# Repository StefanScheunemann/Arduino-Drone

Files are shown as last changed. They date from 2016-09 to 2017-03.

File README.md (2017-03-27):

# Arduino-Drone
Eine Anleitung für den Bau eines Quadrocopters

##Inhalt  
[1. Vorwort](#Vorw)  
[2. Quellen](#Quel)  
[3. Teileliste](#Teil)  
[4. Zusammenbau](#Zusa)  
[5. Code](#Code)  
[6. PID-Kalibrierung](#PID)  
[7. Erster Start](#Erst)  
[8. Fehlercodes](#Fehler)  

###1. Vorwort
Dieser Quadrocopter ist im Rahmen eines Schulprojekts entstanden.  
Es handelt sich nicht um ein professionelles, komplett ausgereiftes Industrieprodukt und Fehler im Code sind zu erwarten. Im Umgang mit der Drohne rate ich zu großer Vorsicht. Es können durch den Quadrocopter ernsthafte Verletzungen und Schäden zugefügt werden, [hier eine realistische Einschätzung zu den Gefahren](http://www.technik-consulting.eu/Analyse/Gef%C3%A4hrdung_Drohne.html). Diese Anleitung beinhaltet Alles, was man wissen muss, um einen Quadrocopter zu bauen. Fehler oder Ungenauigkeiten können aber enthalten sein. In den Quellen können genaue Angaben gefunden werden, von welchen Stellen Code und Rahmen übernommen wurden.  

<h2>2. Quellen</h2>
<p>Der Code stammt von Herrn Brooking, eine Erklärung zu diesem und der Download können auf seiner <a href="http://www.brokking.net/ymfc-al_main.html/">Website</a> gefunden werden. Auf dieser befindet sich eine Erkärung für die Drohne.<br>
Der Code ist nicht mein Gedankengut, alle Rechte gehören Herrn Brooking. Auch die schematic für den Schaltkreis in der Drohne stammt nicht von mir und kann auf der angegebenen Webstite gefunden werden.<br>
Das verwendete 3D-Modell für den Rahmen des Quadrocopters kann auf Thingiverse <a href="http://www.thingiverse.com/thing:264955/#files">hier</a> gefunden werden, es ist für jeden frei verfügbar.<br>
Das Modell wurde nicht von mir erstellt.</p>

###3. Teileliste
In meinem Fall ist das gesamte Drohnengestell mithilfe eines 3D Druckers entstanden.  
Die dafür nötigen 3D Modelle sind repository enthalten und können frei verwendet werden. Wer keinen 3D Drucker zur Verfügung hat, kann ein fertiges Gestell kaufen, oder aus anderen Materialien selber eins bauen. Zu diesem Thema gibt es im Internet eine reichhaltige Menge an Informationen, die jederzeit abrufbar sind.  
  
Die Hardware, die benötigt wird:  
* [Arduino Uno](https://www.arduino.cc/en/Main/arduinoBoardUno)
* [Gyroscope](http://www.dx.com/p/gy-521-mpu6050-3-axis-acceleration-gyroscope-6dof-module-blue-154602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)
* [Brushless Motor + ESC combo](http://eud.dx.com/product/a2212-1000kv-brushless-motor-w-30a-brushless-esc-1045-propeller-dji-f450-550-844413446)
* [Lithium Akku](http://eud.dx.com/product/11-1v-2200mah-30c-li-polymer-battery-pack-for-450-helicopter-dji-phantom-1-450-quadcopter-844366131)
* [Akku Ladegerät](http://www.dx.com/p/b3ac-2s-3s-lipo-balance-charger-black-ac-100-240v-103589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)
* [Fernsteuerung + Empfänger](http://eud.dx.com/product/flysky-fs-t6-2-4ghz-6-ch-2-9-lcd-tx-transmitter-rx-receiver-radio-control-system-black-8-x-aa-844178448)
* Widerstände: [330](https://www.conrad.de/de/metallschicht-widerstand-330-axial-bedrahtet-0207-06-w-yageo-mf0207fte52-330r-1-st-1417595.html), [1k](https://www.conrad.de/de/metallschicht-widerstand-1-k-axial-bedrahtet-0207-06-w-yageo-mf0207fte52-1k-1-st-1417606.html), [1,5k](https://www.conrad.de/de/metallschicht-widerstand-15-k-axial-bedrahtet-0207-06-w-1-st-423386.html)
* [Schrumpfschlauch](https://www.amazon.de/ChiliTec-12000058-Chilitec-Schrumpfschlauch-Sortiment-100-teilig/dp/B003H9CJ1Y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) (nicht zwingend nötig, hilft aber beim Isolieren)

###4. Zusammenbau<a name="Zusa"><a/>
Zuerst wird der Rahmen des Quadrocopters zusammengebaut.  
Jeder Rahmen ist unterschiedlich aufgebaut. Im Fall des beigelegten Rahmens ist der Aufbau leicht verständlich. Es ist sinnvoll, die untere Platte vorerst nicht zu befestigen, da es dann einfacher ist, die Elektronik einzubauen.  
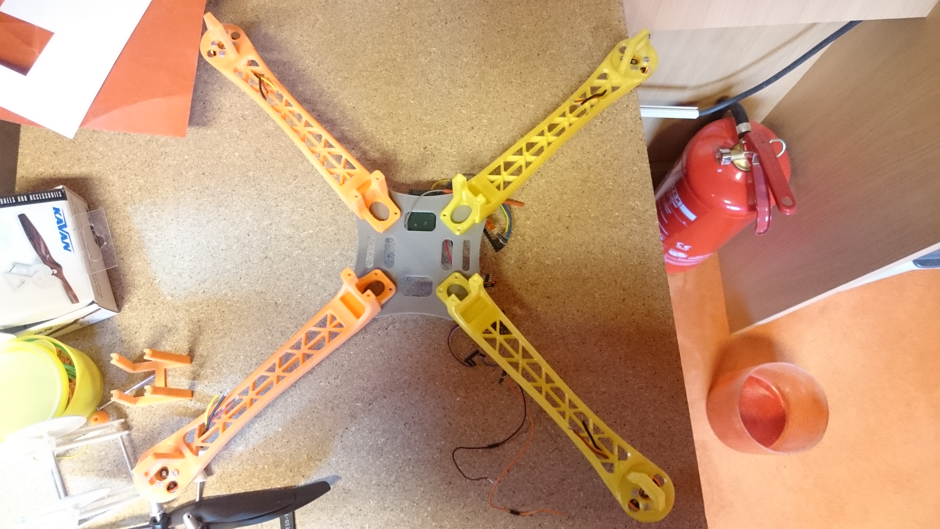
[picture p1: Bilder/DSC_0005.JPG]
  
Sobald der Rahmen zusammengesetzt ist, kann die Hardware verbaut werden.
Der Quadrocopter kann mit den Teilen aus der [Teileliste](#Teil) gebaut werden, aber auch äquivalente Bauteile sollten funktionieren.  
Bei der Verkabelung ist darauf zu achten, dass die schematics beachtet werden, da es sonst später zu Fehlfunktionen kommen kann.  
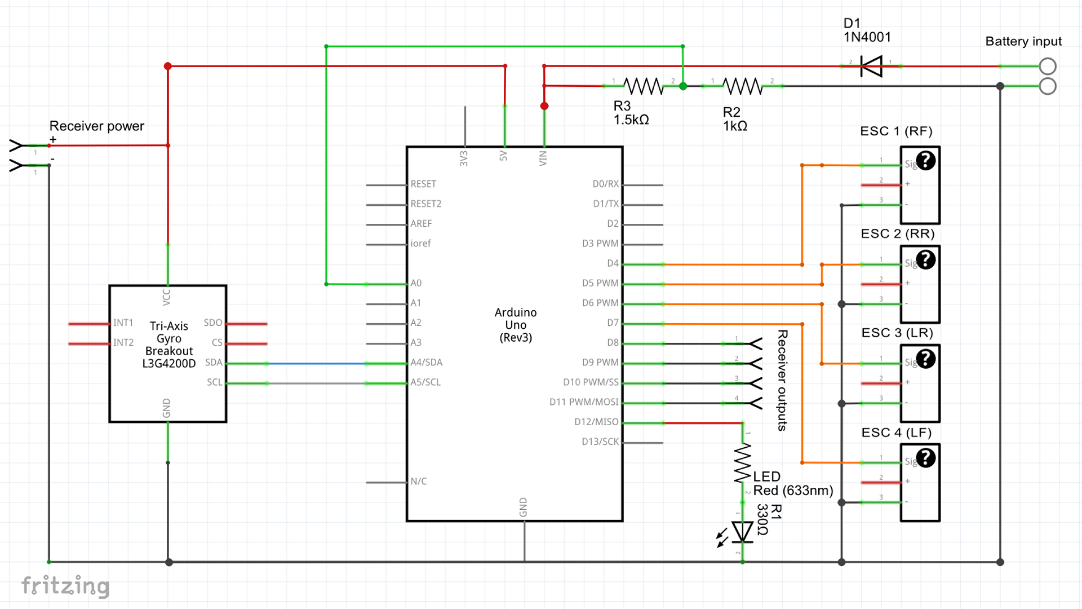
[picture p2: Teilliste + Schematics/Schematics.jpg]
  
Es ist am einfachsten, mit den ESCs zu beginnen.
Diese sollten möglichst weit vom Zentrum entfernt sein, da sie sonst später das Gyroskop stören könnten.
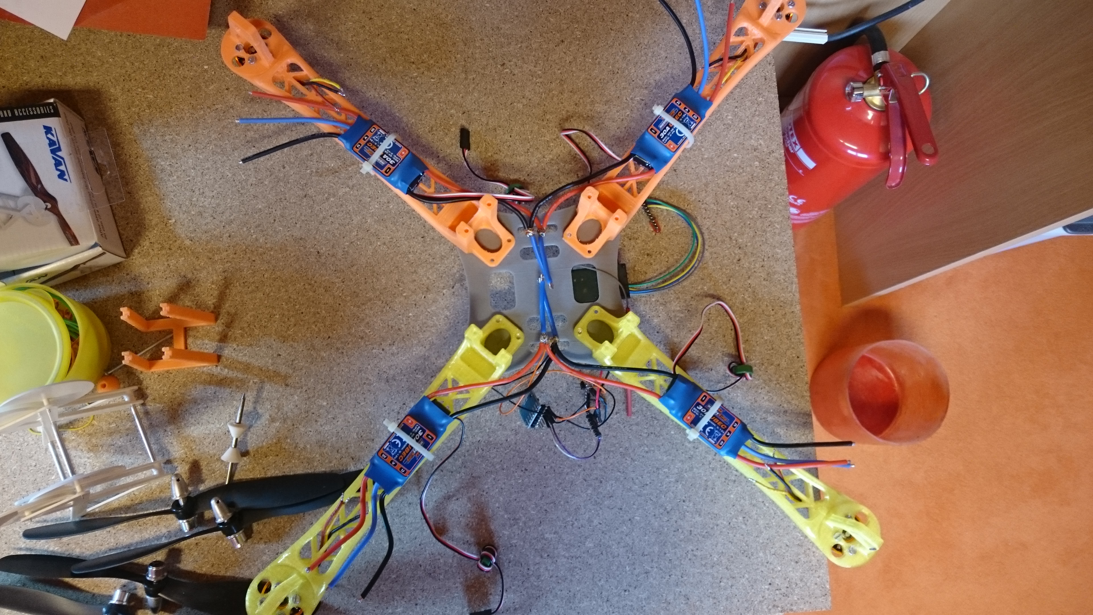
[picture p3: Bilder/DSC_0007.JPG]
  
Sobald die ESCs befestigt sind, dreht man den Rahmen um und befestigt nur das Gyroskop und den Empfänger. Doppelseitiges Klebeband ist für diesen Zweck geeignet. Die Kabel an diesen Teilen sollten schon vor dem Befestigen am Rahmen festgelötet werden, da dies anderenfalls schwierig werden könnte.  
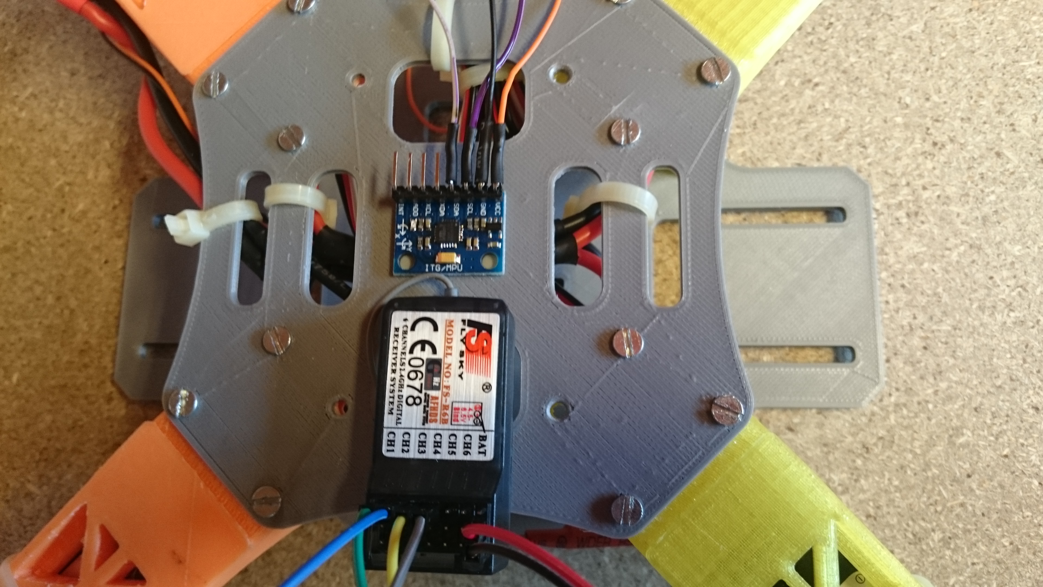
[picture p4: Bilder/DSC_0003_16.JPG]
  
Im nächsten Schritt wird das Arduino befestigt. Wie genau das Arduino am Rahmen befestigt werden kann, muss jeder an seinem eigenen Rahmen überprüfen. Wenn der Rahmen aus den 3D Modellen verwendet wird, ist eine spezielle Platte für diesen Zweck enthalten.  
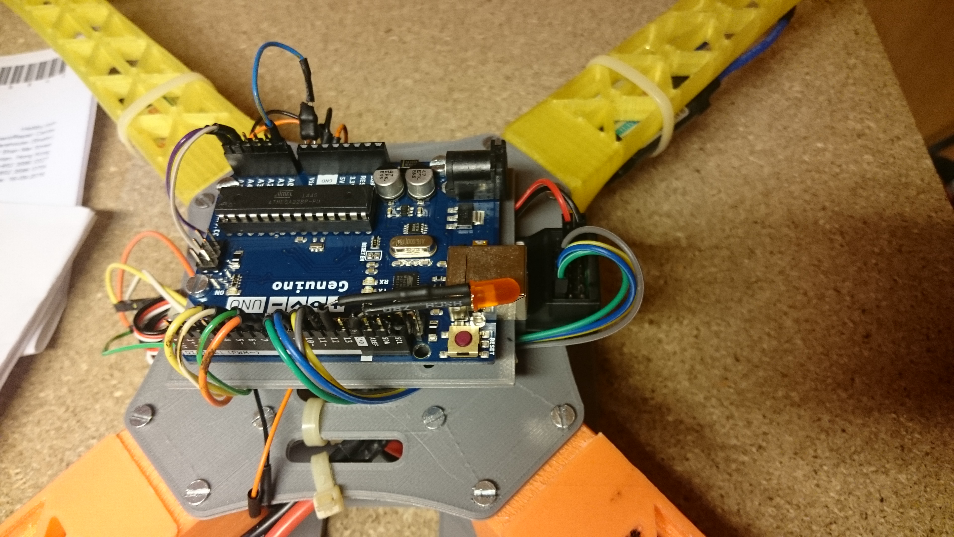
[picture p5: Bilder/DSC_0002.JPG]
  
Als Letztes werden die Motoren befestigt. Dabei muss auf die Rotationsrichtung geachtet werden. Brushless Motoren besitzen drei Ausgänge, ein rotes Kabel, welches den Pluspol darstellt, ein schwarzes Kabel, welches den Minuspol darstellt und ein drittes Kabel als Erdung, häufig gelb. Uns interessieren das Plus- und das Minuskabel. Wenn man Positiv mit Positiv am ESC verbindet und Negativ mit Negativ, dreht sich der Motor im Uhrzeigersinn. Wenn Positiv mit Negativ und Negativ mit Positiv verbunden wird, dreht sich der Motor  gegen den Uhrzeigersinn. In allen Fällen muss auch das dritte Kabel angeschlossen werden. Dies sollte immer an sein Äquivalent des ESCs angeschlossen werden.  
Es muss darauf geachtet werden, dass die Richtungen der Motoren stimmen, da der Quadrocopter später sonst nicht fliegen kann. 
  
| Motor | Bezeichnung | Richtung |
|---|:---:|:---:|
| vorne rechts  | Motor 1 | Uhrzeigersinn |
| hinten rechts | Motor 2 | gegen Uhrzeigersinn |
| hinten links  | Motor 3 | Uhrzeigersinn |
| vorne links | Motor 4 | gegen Uhrzeigersinn |  
  
In der Praxis sieht es wie auf den folgenden Bildern aus.  
Uhrzeigersinn  
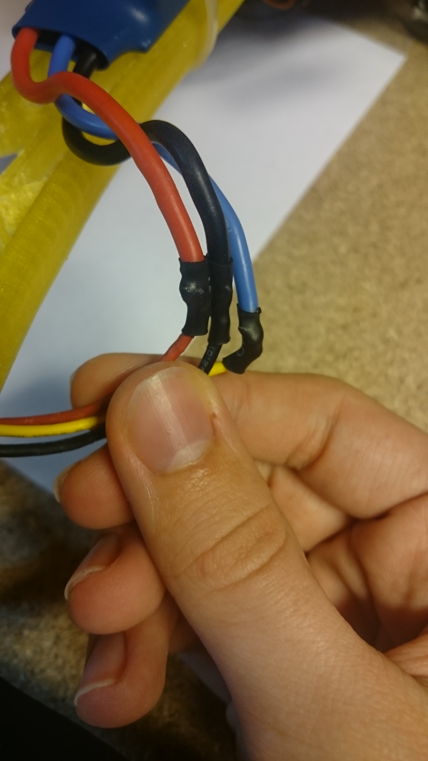
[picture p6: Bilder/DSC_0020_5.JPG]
  
Gegen Uhrzeigersinn  
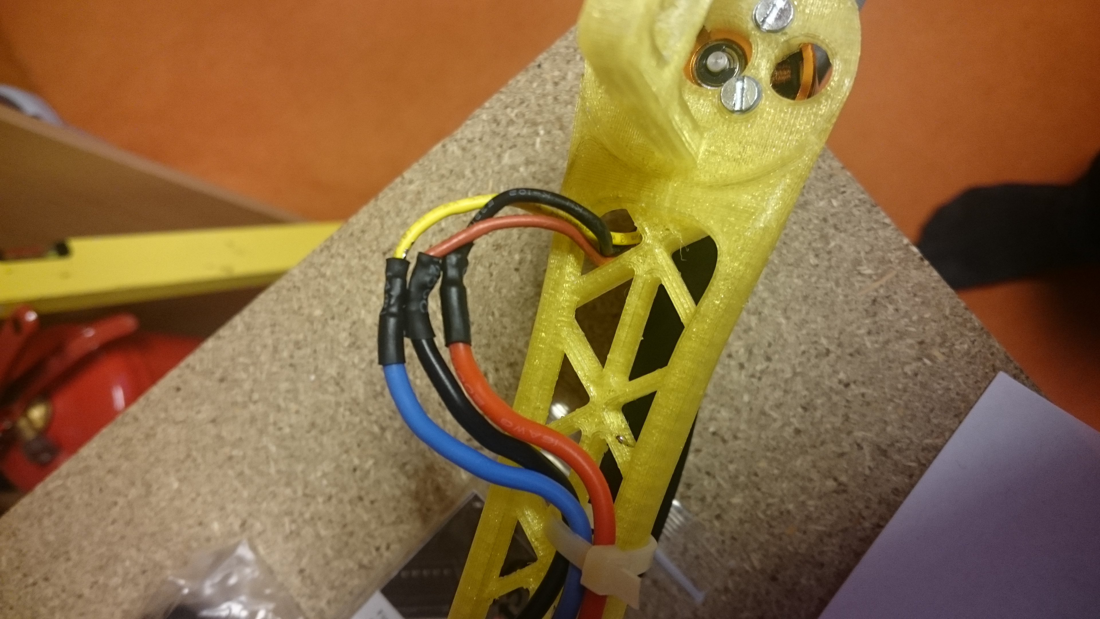
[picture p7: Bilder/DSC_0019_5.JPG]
  
  
Jetzt ist die gesamte Hardware verbaut. Im nächsten Schritt wird diese verkabelt.  
Ich empfehle, alle Verbindungen zu löten, da so eine feste Verbindung entsteht. Aber auch z.B. Kabelhülsen funktionieren. In jedem Fall muss sich streng an die schematics gehalten werden!  
Zum besseren Verständis der Verbindungen  
Verbindung der ESCs, falls der Rahmen kein PDB (power distribuition board) enthält  
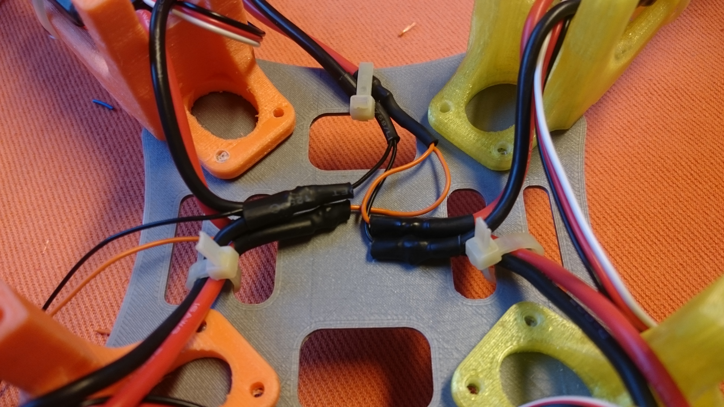
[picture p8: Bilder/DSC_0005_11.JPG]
  
Kabel am Arduino  
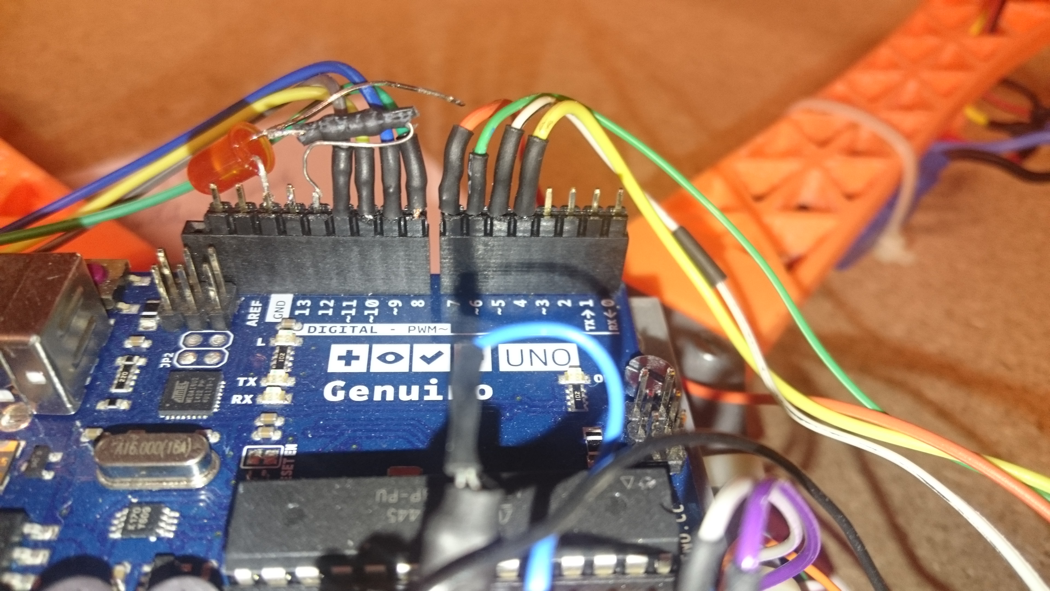
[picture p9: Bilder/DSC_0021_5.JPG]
  
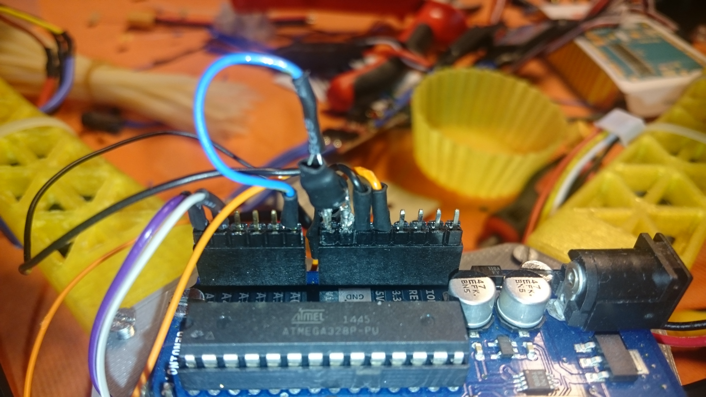
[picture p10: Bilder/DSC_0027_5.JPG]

  
Abschließend ist es von Vorteil, über das Arduino einen Schutz anzubringen, damit es nicht ungeschützt beim Transport bzw. Flug ist. Bei den 3D Modellen liegt ein derartiger Schutz bei, ob man diesen verwendet oder selber etwas anderes baut, spielt keine große Rolle, solange es gegen Einwirkungen von außen schützt.  
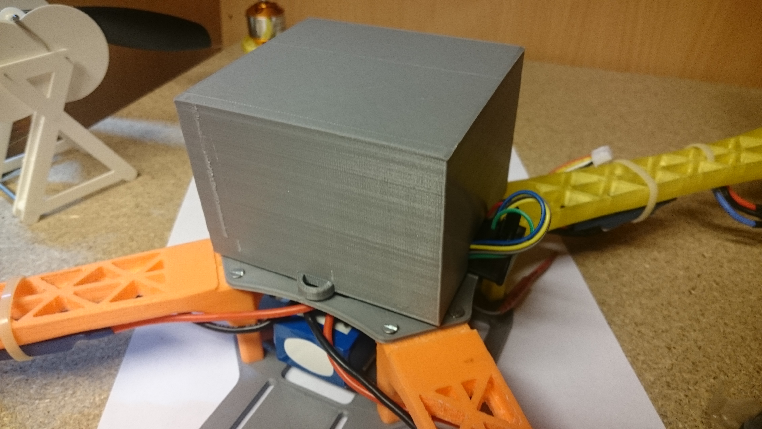
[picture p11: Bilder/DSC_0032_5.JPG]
  

###5. Code<a name="Code"><a/>
Um die Drohne verwenden zu können, werden drei Arduino Sketches benötigt.  
[1. Setup](#Setup)  
[2. Calibration](#Calib)  
[3. Flight Controller](#Flight)  
  
Der erste Sketch ist ein Setup, in dem alle Bauteile der Drohne überprüft werden und sowohl die Fernbedienung, als auch das Gyroskop für das Arduino kalibiriert werden. Die Ergebnisse der Kalibrierungen werden im EEPROM, dem Speicher des Arduinos, gespeichert. Das Programm läuft über den seriellen Monitor des Arduinos.    
Der zweite Sketch wird verwendet, um die Ergebnisse der Kalibrierung zu testen. Im seriellen Monitor können durch bestimmte Befehle unterschiedliche Daten aufgerufen werden. Darauf gehe ich aber erst im letzten Teil dieser Anleitung ein, da dies sonst zu umfangreich wird: [Der erste Start](#Erst).  
Der dritte Sketch ist der flight controller. Mit diesem wird die Drohne letztlich gesteuert. Es ist eine Sicherungsfunktion enthalten. Aber trotzdem sollte beim Start immer ein Sicherheitsabstand eingehalten werden.  
Alle diese drei Sketches müssen vom Ersten bis zum Dritten auf den Arduino geladen werden, ausgeführt werden und nur wenn keine Fehler während der Prgrammabläufe auftauchen, darf das Nächste installiert werden. Bei Nichtbeachtung der Reihenfolge kann es zu schweren Fehlern kommen.  
  
Zum Grundverständnis erkläre ich an dieser Stelle erstmal, wie der Quadrocopter seine Position und die Befehle der Fernbedienung "versteht". Im folgenden Text wird häufig von einem Puls zwischen 1000 und 2000 gesprochen. Dieser Puls bedeutet eigentlich nur, dass die Fernbedienung die Befehle mit einer Frequenz von 1000 bis 2000 Hertz an den Empfänger sendet. Das Arduino rechnet auch mit dieser Frequenz. Es wäre auch möglich, dies in ein kleineres Format im Arduino für die Rechnungen umzuwandeln. Das Ergebnis wäre aber dasselbe und würde innerhalb des Codes zu Verwirrung führen. Während des Setups wird auch an die ESCs diese Frequenzreichweite übertragen, da diese auch mit Pulsen arbeiten. Wenn eine Reichweite von 1000 mögliche Pulsen existiert, ist auch eine sehr genaue Bestimmung der Werte möglich und sehr genaue Ergebnisse können innerhalb des Codes produziert werden.  
Die Werte 1000 bis 2000 sind also nicht frei erfunden und nur als Variablen festgelegt, sondern durch die Fernbedienung definiert und müssen so verwendet werden.  
  
Der gesamte Code kann eingesehen und modifiziert werden. Der Code ist durch viele Kommentare verständlich gemacht. Inwiefern Modifikationen sinnvoll sind und wo diese vorgenommen werden sollten, wird im späteren Verlauf dieser Dokumentation aufgegriffen.  
Direkte Weiterleitungen zum Code:  
  
[Setup](https://github.com/StefanScheunemann/Arduino-Drone/tree/master/Code/Setup)  
[Calibration](https://github.com/StefanScheunemann/Arduino-Drone/tree/master/Code/Calibrate)  
[Flight controller](https://github.com/StefanScheunemann/Arduino-Drone/tree/master/Code/Flight_controller)  
  
####Setup<a name="Setup"><a/>
Im Setup wird die gesamte Hardware für das Arduino kalibriert. Um dies zu tun, muss der Setup-Sketch auf den Arduino geladen werden und am PC im Arduino-Programm der serielle Monitor geöffnet werden. Im seriellen Monitor muss die Baudrate auf 57600 eingestellt werden für diesen Vorgang.  
Falls während des Setups Fehler auftreten, wird ein Fehlercode angezeigt. Jeder Fehler ist dokumentiert und mit Lösungen versehen. Diese Lösungen werden im späteren Verlauf dieser Anleitung dokumentiert. [Abkürzung zu Fehlercodes](#Fehler)  
Nun wird ein Programm Ablauf gezeigt, dem man als Nutzer nur folgen und die Befehle befolgen muss.  
Zuerst werden die Endposition der Fernbedienung kalibriert. Dabei ist zu beachten, dass "nose down" auf dem rechten Steuerknüppel "nach unten" bedeutet. Wenn der Quadrocopter seine Nase hoch zieht, bewegt der Quadrocopter sich nach hinten.  
Sobald die Kalibrierung der Fernbedienung abgeschlossen ist, beginnt die Kalibrierung des Gyroskops. Zu diesem Zweck wird das Programm den Nutzer dazu auffordern, den Quadrocopter in bestimmte Positionen zu bewegen. Dabei muss darauf geachtet werden, dass die richtigen Seiten bewegt werden, da es sonst später zu Fehlern kommen kann.  
Der letzte Schritt ist die Kontrolle der Status-LED. Diese sollte aufleuchten, wenn der Befehl dazu im seriellen Monitor angezeigt wird. Prinzipiell ist die LED nicht nötig. Falls aber später Probleme auftreten, kann an der Blinkfrequenz erkannt werden, um welchen Fehler es sich handelt. Die LED erfüllt somit eine wichtige Rolle.  
  
Nun sollte das Programm anzeigen, dass der Vorgang beendet ist und der serielle Monitor kann geschlossen werden.  
An dieser Stelle ist das Setup abgeschlossen. Es kann zum nächsten Schritt übergegangen werden.  
Wer aber noch daran interessiert ist, wie der Code aufgebaut ist und wie die Informationen im EEPROM gespeichert werden, kann den Code frei verwenden und modifizieren, alle Informationen sind Open Source und es darf daran alles verändert werden. Doch macht es in diesem Sketch wenig Sinn, etwas zu modifizieren.  
Im späteren Verlauf wird das Modifizieren noch wichtiger.  
Der Code ist zum besseren Verständis mit Kommentaren versehen. Es sollte nicht nötig sein, sich aufwändig einlesen zu müssen, um den Inhalt zu verstehen.  
  
#####Calibration<a name="Calib"><a/>
Das zweite Programm, welches installiert werden muss, ist die Kablibrierung.  
Dieser Sketch unterscheidet sich stark vom Setup. Es wird nichts auf dem EEPROM verändert.  
Sobald der Sketch auf den Arduino geladen ist, muss wieder der serielle Monitor geöffnet werden. Es wird weiterhin die Baudrate 57600 verwendet.  
Nun gibt es mehrere Befehle, die ausgeführt werden können, zum Überprüfen der Funktionen des Gyroskops, der Fernbedienung und der Schwingungen der Motoren.  
Wenn in den seriellen Monitor **a** eingegeben wird, zeigt der serielle Monitor die Position des Gyroskops. Zu beachten ist, dass Yaw bedeutet, inwieweit der Quadrocopter auf dem Boden gedreht wurde. Sobald die Drehung beendet ist, setzt der Wert für Yaw sich selbstständig auf 0 zurück. Es sollte eine perfekte Nullstellung erreicht werden, da der Quadrocopter sonst nie ruhig in der Luft stehen kann.  
  
Als nächstes wird in den seriellen Monitor **r** eingegeben. Mit diesem Befehl werden die Daten der Fernbedienung aufgerufen. Im seriellen Monitor werden nun vier unterschiedliche Daten angezeigt.  
  
Die Werte sollten sich zwischen 1000 und 2000 befinden, der Anstieg/Abfall der Werte sollte gleichmäßig sein und nicht springen, da es sonst später zu Problemen kommen kann. Minimale Abweichungen sind unproblematisch. Es sollten nur keine großen Abweichungen sein.  
  
Mit den Befehlen **1-5** kann entwededer von jedem Motor einzeln die verursachte Vibration überprüft werden. Zu diesem Zweck sollte auf den Motoren ein Propeller befestigt werden. Im Idealfall liegt die Vibration unter 50. Dies ist kein Referenzwert, der mit anderen Werten verglichen werden kann. Der Test sollte bei 50 % Beschleunigung ablaufen. In dieser Position sollte der Quadrocopter knapp nicht abheben und es werden gute Ergebnisse erzeugt. Bei diesem Test ist größte Vorsicht geboten, der Quadrocopter kann schwere Verletzungen zufügen und es sollten mindestens **fünf Meter** Sicherheitsabstand eingehalten werden; ideal sind **zehn Meter**.
  
| Motor	 | Command |
|---|:---:|
| Motor 1	  | 1 |
| Motor 2 | 2 |
| Motor 3	  | 3 |
| Motor 4	  | 4 |
| Motor 1-4 | 5 |
  
####Flight Controller<a name="Flight"><a/>
Das dritte Programm ist das, dass letztendlich für das Fliegen verwendet wird. Dieser Sketch greift auf die Daten, die im EEPROM abgelegt wurden, zurück und verwendet sie als Grundlage der Berechnungen für die Stabilität. Die vorherigen Schritte müssen genau befolgt werden, da sonst Fehler beim Flug entstehen können.  
  
Das Gyroskop gleicht beim Flug permanent den Quadrocopter aus, sodass zu keinem Zeitpunkt, wenn kein Befehl, abgesehen von der senkrechten Beschleunigung, übertragen wird, der Quadrocopter in eine nicht horizontale Position gerät.  
Der Ablauf im Sketch hinter dieser Mechanik ist, dass das Gyroskop permanent die Position des Quadrocopters überprüft. Im Sketch ist festgelegt, dass in der Nullstellung des Gyroskops und der Fernbedienung ein Puls von 1500 an die ESCs gesendet wird. Nullstellung bedeutet, dass der Quadrocopter senkrecht zum Boden ausgerichtet ist. Die ESCs sind auf die Frequenz von 1000 bis 2000 kalibiriert.  
Wenn nun der Winkel, in dem sich der Quadrocopter relativ zum Boden befindet, verändert wird, rechnet das Arduino eine definierte Antisteigung aus; also die aktuelle Position abgezogen von der Standardposition und ermittelt einen Gegenimpuls, der an die ESCs geschickt wird.   
Im Sketch ist festgelegt, dass wenn die senkrechte Beschleunigung, also der linke Steuerknüppel, in der untersten Position ist, der Quadrocopter 0 % Motor-Output aufbringt. Der Output steigt linear bis auf 100 % in Maximal-Stellung an. Wichtig ist dabei zu wissen, dass bei 50 % der Quadrocopter stabil in der Luft steht und weder steigt noch sinkt. Bei unter 50 % wird ein Absinken und bei über 50 % ein Ansteigen zu beobachten sein. Falls dies nicht richtig funktioniert, müssen die Fernbedienung und der Quadrocopter neu kalibriert werden. Das Kalibrieren des Quadrocopters muss erneut über das Setup durchgeführt werden und sollte nicht übersprungen werden.   
  
Wenn der Quadrocopter sich also in der Ausgangslage befindet, wird ein Puls von 1500 an den PID-controller gesendet (dieser wird im [nächten Teil](#PID) genauer erklärt) und es wird keine Veränderung vorgenommen. Wenn nun aber auf der Fernbedienung der Befehl Roll gegeben wird mit halber Beschleunigung, also der rechte Steuerknüppel 50 % nach rechts gedrückt wird, so wird der Wert auf 1750 erhöht. Nun kippt der Quadrocopter kontinuierlich nach rechts. Das Gyroskop nimmt diese Veränderung der Lage wahr und rechnet seine eigene Rechnung dagegen. Im Code ist festgelegt, das für jeden 1°, den der Quadrocopter gekippt ist, ein Puls von 15 gegengerechnet wird. Wenn beim Rollen nun also 5° erreicht sind, wird gegen die 1750, die von der Fernbedienung ausgegeben werden und vom Arduino verwendet werden, ein Wert von 75 gegengerechnet. Der interne Wert für die Position ist nun also 1675. Das Rollen wird soweit weitergeführt, bis der Wert von 1500 erreicht und und der Quadrocopter damit seine Zielposition, die er immer erreichen möchte, erreicht hat. Dieser Fall tritt in diesem Fall bei 16,7° ein. Wenn man also den Befehl fürs Rollen mit 50 % Leistung gibt, wird der Quadrocopter bis auf 16,7° kippen und in dieser Position bleiben, bis ein neuer Befehl von der Fernbedienung gegeben wird. Maximal möglich sind 33,3°. Dieser Wert wird als allgemein sicher anerkannt und führt zu guter Beschleunigung und gut kontrollierbarem Flugverhalten. Weiteres Rollen würde zu höherer Beschleunigung führen, aber auch die Gefahr eines Überschlags erhöht sich. Diese Werte gelten genauso für Pitch und Yaw, nur die senkrechte Beschleunigung ist nicht von dieser Berechnung betroffen.  
  
Wenn der Maximalwinkel größer/kleiner sein soll, muss am Code eine Veränderung vorgenommen werden. Dies ist in Zeile 14 und 22 des flight controllers möglich. Wenn der Wert erhöht wird, steigt der maximale Winkel. Wenn der Wert verkleinert wird, sinkt der maximale Winkel. Es kann sinnvoll sein, den Winkel zu verkleinern, wenn die Drohne dem Nutzer zu aggressiv reagiert.  
Auch der Standardwert von α=1°=15 kann verändert werden. An diesem Wert zu modifizieren ist eher nicht empfehlenswert, da der Quadrocopter selbst bei kleinen Veränderungen sehr aggressiv reagieren kann. Wenn der Maximalwinkel verändert werden soll, ist es sinnvoller, die vorherige Methode zu verwenden.  
  
Falls der Quadrocopter anders reagiert, als man es erwarten würde und das Problem mit dem Gyroskop in Verbindung stehen könnte, kann die gesamte auto level Funktion deaktiviert werden. Dies ist in Zeile 24 möglich. Es ist wichtig zu bedenken, dass mit dieser Einstellung auf false keine Flugunterstützung mehr existiert. Es muss manuell gegengelenkt werden. Im Allgemeinen rate ich von einem Flug ohne auto level-Funktion ab.  
  
Im flight controller ist noch eine weitere Funktion eingebaut, die die LED verwendet.  
Die LED zeigt einen niedrigen Akkustand an, indem sie beginnt, durchgehend zu leuchten. Die Funtion dafür befindet sich in Zeile 250.   Wenn die output-Spannung des Akkus zu niedrig wird, um die Motoren mit ausreichend Energie versorgen zu können, beginnt die LED permanent zu leuchten. Diese Warnung bedeutet nicht, dass der Quadrocopter nicht mehr fliegen kann. Er sollte aber in absehbarer Zeit gelandet werden.  

Darüber befindet sich eine Funktion, die es für den Arduino einfacher macht, durch einen komplementären noise filter den Akkustand zu errechnen. Mit diesem treten weniger Ungenauigkeiten beim Errechnen der Spannung des Akkus auf und die LED zeigt nicht schon zu früh einen niedrigen Akkustand an.  
  
Falls noch weitere Unklarheiten bezüglich des flight controllers existieren kann jede Einzelheit [hier](https://github.com/StefanScheunemann/Arduino-Drone/tree/master/Code/Flight_controller) im Code nachgelesen werden. Der gesamte Code ist mit Kommentaren zum besseren Veständnis gefüllt.  

##6. PID Kalibrierung<a name="PID"><a/>
Die PID Werte sind das Erste, was man sehen wird, sollte man den Code des flight controllers öffnen.  
Diese PID Werte sind essentiell für die auto level-Funktion des Quadrocpters, die das Besondere an diesem gesamten Projekt ist. Zum Verständis ist es als erstes sinnvoll zu verstehen, wofür PID steht. Wer schnell zu dem Teil springen möchte, in dem erklärt wird, wo und wie man diese Werte anpassen sollte, wird [hier](#PIDmod) weitergeleitet.  
  
####Theoretische Erklärung der PID-Werte  
  
**P** steht für proportinal, an dieser Stelle wird **Output des Gyroskops - Output des receivers * P(gain)** gerechnet, oder auch  
(gyro - receiver) * P (gain). Wenn sich nun der Quadrocopter in einer 10°-Lage gekippt zum Boden befindet und 1°=15 => 10*15=150. Nehmen wir nun an, von der Fernbedienung wird kein Befehl gesendet, der eine solche Veränderung der Lage herbeiführt, so wird der Quadrocopter nun versuchen, in die Standardposition von 1500 zurück zu kehren. Aus der Rechnung ergibt sich also, dass der aktuelle Wert 1650 entspricht, aber 1500 angepeilt werden. Theoretisch sollte diese Funktion ausreichen, um den Quadrocopter in eine stabile Position zu bringen. Wenn man aber nur diese Funktion verwendet, so wird man feststellen, dass der Quadrocopter anfängt, gleichmäßig zu schwingen. Bei jeder Korrektur wird der Quadrocopter von selbst übersteuern und nie in eine ruhige Position kommen. Um dieses Problem zu lösen werden weitere Funktionen eingebracht, die auf einer anderen Basis den Quadrocopter stabilisieren.  
  
**I** steht für Intergral, in dieser Funktion wird  
I(output) + ((gyro - receiver) * I(gain). Wenn man nun also wieder von 10° relativer Steigung Nullpunkt ausgeht, dann wird bei einem Wert von I = 1 die Rechnung I(output), jetzt noch 0 + ((150 - 0), da von der Fernbedienung kein Befehl gesendet wird, * I(gain), was als 1 definiert wurde, gerechnet und es kommt ein Ergebnis von 150 raus, was der Korrketur entspricht, die ausgeführt werden muss.  
In der nächsten Rechnung wird 150(der output der letzten Rechnung) + ((150 - 0) * I(gain, was als 1 definiert bleibt), gerechnet.  
Im Ergebnis bedeutet dies, dass selbst wenn die Steigung konstant ist und der Winkel nicht verändert wird, die Korrektur immer stärker wird, bis wieder der Nullpunkt erreicht ist, an der der errechnete Wert wieder auf 0 zurücksetzt wird, da sobald der Winkel = 0° ist und von der Fernbedienung kein Befehl gesendet wird, das Ergebnis der Rechnung gleich 0 ist.  
Wenn nur diese Rechnung verwendet wird, kann wieder festgestellt werden, dass der Quadrocopter überkompensiert und somit immer noch keine stabile Haltung in der Luft erreicht werden kann. Der Quadrocopter wird mit nur dieser Funktion, ähnlich wie bei der ersten von einer Seite zur anderen schwingen. Doch dies passiert deutlich langsamer. Um nun eine stabile Position zu erreichen, ist eine weitere Funktion nötig, die das Überkompensieren verhindert.  
  
**D** steht für Derivative, diese Funktion unterscheidet sich von den vorherigen, als dass sie nur auf eine Veränderung eine einmalige Korrektur ausgibt und nicht, wie die anderen Funktionen, konstant gegen die Steigung gegenarbeitet.  
(gyro - receiver - gyro(prev) - receiver(prev)) * D(gain). Wenn man nun wieder davon ausgeht, dass D = 1 definiert ist, dann ergibt sich bei einer Steigung von 10° im Intervall davor eine Steigung von 0°
(150 - 0 - 0 - 0) * 1, das Ergebnis wäre eine Korrektur von 150. Wenn man nun aber im nächsten Messintervall weiterhin die Position von 10° verwendet, dann ergibt sich  
(150 - 0 - 150 - 0) * 1, das Ergebnis dieser Rechnung wäre 0. Diese Funktion verursacht also nur eine Korrektur, wenn die Position zwischen zwei Intervallen sich verändert, ansonsten ist das Ergebnis immer 0.  
Wenn nun durch die anderen beiden Funktionen eine Überkompensation stattfindet, dann sendet diese Funktion eine einzelne Korrektur, die den Quadrocopter wieder ausgleicht und in die waagerechte Position regelt.  
  
Um es anschaulicher zu machen habe ich eine Google-Tabelle mit den Rechnungen erstellt. Die Diagramme zeigen die Korrekturbefehle, die von den Funktionen gesendet werden. Auch kann das Dokument heruntergeladen werden und mit den PID-Werten experimentiert werden, wie diese sich verändern, wenn die gain-Werte verändert werden. In dem Dokument liegen zwischen jedem Messungsinvtervall 4 Millisekunden. Mit diesem Wert arbeitet auch das Arduino im flight controller. Die Rechnungen des PID controllers finden im flight controller in Zeile 424 statt, das Verändern der PID-Werte wird aber in Zeile 9 - 11 durchgeführt.  
  
**[Link zur Tabelle](https://docs.google.com/spreadsheets/d/1bJNEvERLeVwe6B2JFlEnVjHe6nW1A6QOTmVpb9kBsjY/edit?usp=sharing)**  
  
Praktische Anwendung der PID Werte<a name="PIDmod"><a/a>  
  
Wenn man nun weiss, wie der PID controller funktioniert, kann man beginnen, die gain-Werte zu modifizieren.  
Jeder Quadrocopter hat eine andere Struktur und reagiert anders auf die Korrekturen. 
Deswegen **müssen** die PID-Werte manuell angepasst werden und nach jedem Umbau oder größerer Reperatur muss die Kalibrierung neu erfolgen.  
Die im Programm angegebenen PID-Werte sind nicht allgemein gültig. Mein Quadrocopter funktioniert mit diesen aber am besten.  
  
Für die folgende Prozedur empfehle ich, im ersten Teilschritt bei der Kalibrierung des D-Wertes Sicherheitshandschuhe anzuziehen, um Verletzungen zu vermeiden.  
  
Um die Kalibrierung zu beginnen, müssen im flight controller die PID-Werte für roll, Zeile 9 bis 11) auf 0 gesetzt werden. Die Kalibrierung verläuft am besten, wenn man mit dem D-Wert beginnt. Dies tut man, indem in Zeile 11 der Wert für D nun von 0 auf 3 erhöht wird. Mit dieser Veränderung wird der Sketch auf den Quadrocopter übetragen. Nun greift man den Quadrocopter fest in der Mitte und beginnt den Schub zu erhöhen. Der Schub wird solange erhöht, bis der Punkt erreicht ist, an dem der Quadrocopter **fast** vom Boden abhebt. Jetzt muss der Quadrocopter in alle Richtungen geneigt werden, der Quadrocopter sollte sich stabil anfühlen und nicht ruhelos. Nun erhöht man den D-Wert immer weiter in Schritten von 1 und testet jedes Mal, bis der Quadrocopter sich unruhig anfühlt und beginnt, sich ungleichmäßig zu verhalten. Die Unruhe sollte bei +-20 einsetzen. Wenn dieser Punkt erreicht ist, zieht man vom D-Wert 25 % wieder ab und erhält einen Wert, bei dem der Quadrocopter sich ruhig verhält.  
  
Als nächstes wird dieser Vorgang für den P-Wert wiederholt. Statt einer Erhöhung von 1 pro Versuch, sollte diesmal eine Steigerung von 0.2 verwendet werden. An diesem Punkt muss der Quadrocopter auch nicht mehr in der Hand gehalten werden. Auf einer Grasfläche kann vorsichtig geflogen werden. Wenn wieder der Punkt erreicht ist, an dem der Quadrocopter sich unruhig verhält, wird der Wert um 50 % reduziert und erhält somit einen stabilen P-Wert.  
  
Im letzten Schritt wird der I-Wert erhöht. Dies findet in Schritten von 0.01 statt. Man wird feststellen, dass der Quadrocopter immer stabiler fliegt. Wieder wird der Quadrocopter ab einem bestimmten Wert sich unruhig verhalten. An diesem Punkt wird der I-Wert wieder um 50 % reduziert.  
  
Wenn diese Kalibrierung abgeschlossen ist, erhält man einen stabil fliegenden Quadrocopter. Es darf aber nicht vergessen werden, dass nach jedem Umbau und jeder Reparatur diese Prozedur wiederholt werden sollte.  

##7. Erster Start<a name="Erst"><a/>
Sobald der Sketch auf dem Arduino gespeichert ist, ist die Drohne flugbereit. Beim Start gilt es bestimmte Dinge zu beachten:  
1. Um den Quadrocopter zu starten, muss an der Fernbedienung der throttle stick in die untere, linke Ecke bewegt werden. Erst ab diesem Moment ist Sicherung deaktiviert.  
2. Um den Quadrocopter auszuschalten, muss der throttle stick in die untere, rechte Ecke bewegt werden. Dies löst die Sicherung aus und keine weiteren Befehle werden umgesetzt.  
3. Sobald die Sicherung deaktiviert ist, muss der Quadrocopter gestartet werden. Die ersten Sekunden ist der Ausgleich durch das Gyroskop deaktiviert, sodass die Drohne senkrecht starten kann. Sie gleicht sich erst in der Luft aus. Auch sollte insofern zügig gestartet werden, damit ein schnelles Abheben auf mindestens 20 Centimeter gewährleistet ist und die Drohne sich nicht am Boden verfangen kann.
4. Vor und während des Fluges ist ein Sicherheitsabstand einzuhalten. Ein Start aus der Hand ist zwingend zu vermeiden, da durch Windstöße oder Fehler des Programms die Drohne aggressiv reagieren kann und somit den Nutzer schwer verletzen kann.  
5. Es ist durchaus damit zu rechnen, dass erste Flugversuche fehlschlagen. Es sollte von Beginn an eingeplant werden, dass einige Propeller kaputt gehen. Die gegebenen PID-Werte sollten einen stabilen Flug gewährleisten, es können aber dennoch Probleme auftreten. Um diese Probleme zu beheben, müssen die PID-Werte angepasst werden. Wie dies möglich ist, wurde im [vorherigen Teil](#) erklärt.  
6. Die eingebaute LED hat zwei Funktionen. Wenn die LED permanent leuchtet, bedeutet dies, dass der Akku unter 25 % Leistung gefallen ist. Wenn die LED schnell blinkt, konnte keine Verbindung hergestellt werden. In diesem Fall sollte einige Sekunden gewartet werden.  
  
Wenn der erste Flug erfolgreich verlaufen ist, sollten alle Teile des Quadrocopter überprüft werden. Selbst bei einem erfolgreichen Flug können Schäden entstehen. Der Rahmen sollte besonders genau betrachtet werden, da durch die Motoren starke Kräfte auf diesen ausgeübt werden. Falls Risse oder ähnliche Schäden auftreten, müssen diese behoben werden. Es darf nicht mit defekten Teilen geflogen werden.  
  
Ein derartiger Riss kann zum Beispiel so aussehen  
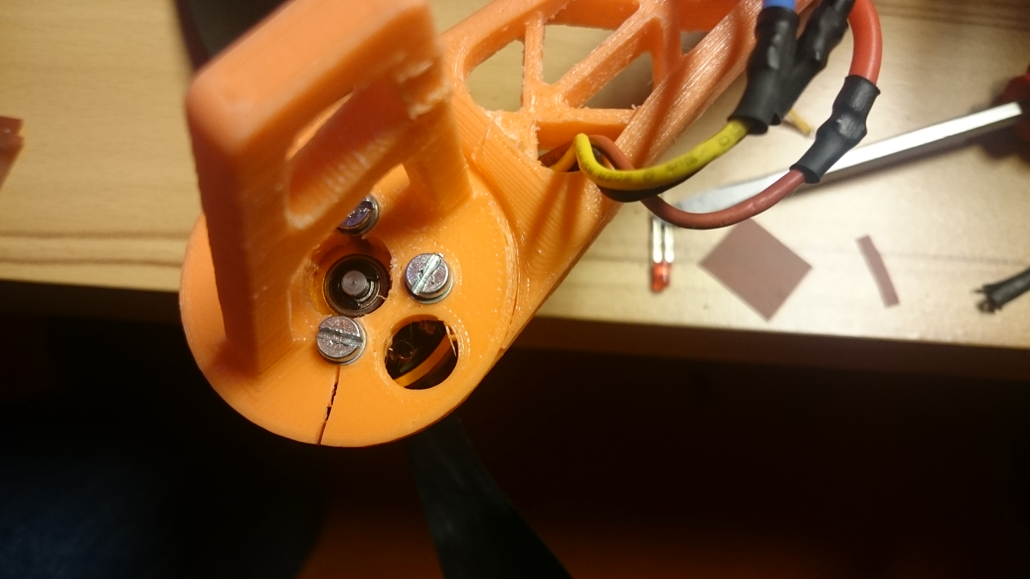
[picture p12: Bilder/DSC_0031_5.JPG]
  

##8. Fehlercodes<a name="Fehler"><a/>
Die Fehlercodes beziehen sich auf das Setup und die Kalibrierung. Jeder mögliche Fehler ist in dieser Sektion dokumentiert.  
  
####Error 1: No valid receiver signals found  
Der Empfänger sendet ungültige Signale. Akzeptiert werden Signale mit einem Puls zwischen 900 und 2100.  
Um das Problem zu lösen, muss überprüft werden, ob der Empfänger richtig mit dem Arduino verbunden ist. Die Channel 1 bis 4 müssen mit den Pins 8 bis 12 verbunden werden. Die Reihenfolge spielt dabei keine Rolle.  
  
####Error 2: No stick movement detected in the last 30 seconds  
Das Arduino registriert keine gültigen Signale von der Fernbedienung.  
Die Fernbedienung sollte aus- und wieder angeschaltet werden und die Steuerknüppel dürfen nicht zu ruckartig bewegt werden.  
  
####Error 3: No gyro device found  
Das Gyroskop kann nicht vom Arduino identifiziert werden.  
Der Sketch funktioniert mit dem MPU 6050. Andere Gyroskope sind nicht getestet. Falls ein anderes Gyroskop verwendet wird, das nicht mit 5 Volt, sondern mit 3,3 Volt kompatibel ist, muss die Stromzufuhr verändert werden.
Falls der Fehler mit dem MPU 6050 auftaucht, muss die Verkabelung an diesem überprüft werden. Diese sollte so aussehen  
  
| Arduino	  | Gyro |
|---|:---:|
| GND | GND |
| 5V | Vin/Vss |
| SDA/A4 | SDA |
| SCL/A5 | SCL |
  
####Error 4: No angular motion is detected in the last 10 seconds  
Wenn der Quadrocopter beim Setup nicht mindestens 30° in die richtige Richtung gekippt wird, entsteht diese Fehlermeldung.  
Innerhalb von 10 Sekunden muss der Quadrocopter auf der angegebenen Seite um 45° gekippt werden. Zu diesem Zweck darf der Quadrocopter nicht bewegt, sondern nur gekippt werden, da die Werte sonst ungültig sind.  
  
####Error 5: EEPROM verification failed  
Sobald das Setup abgeschlossen ist, werden alle gemessenen Daten im internen Speicher des Arduino Uno, dem EEPROM, gespeichert. Sollte dabei ein Fehler auftreten, erscheint diese Meldung.  
Es sollte überprüft werden, ob eine stabile Stromversorgung mit 5 V gewärleistet ist, da es sonst zu Fehlern beim Speichern kommen kann. Wenn der Fehler weiterhin besteht, ist der Speicher des Arduino corrupted und sollte formatiert werden.  
  
####Error 6: Receiver channel verification failed  
Dieser Fehler tritt auf, falls ein Steuerknüppel für mehrere Funktoinen definiert ist.  
Es sollte beim Setup darauf geachtetet werden, dass immer nur ein Steuerknüppel bewegt wird und nicht mehrere gleichzeitig. Sollte das Problem weiter bestehen, muss die Fernbedienung neu kalibriert werden.  
  
####Error 7: Gyro exes verification failed  
Wenn beim Überprüfen der Achsen des Gyroskops an einer Stelle mehrere Achsen gleichzeitg erkannt werden, entsteht dieser Fehler.  
Um diesen Fehler zu vermeiden, sollte beim Setup darauf geachtet werden, dass wenn der Quadrocopter in eine bestimmte Richtung gekippt werden soll, immer nur in genau diese Richtung gekippt wird und nicht in mehrere gleichzeitig.

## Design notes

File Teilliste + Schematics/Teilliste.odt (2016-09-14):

Arduino Uno Quadrocopter: DIY

Gehäuse:

- 4 Arme: je 5h 30min; 43 Gramm

- Untere Platte: 3h 35min; 32 Gramm

- Obere Platte: 1h 56min; 17 Gramm

=> 26h 31min; 221 Gramm; (6,62€)

Hardware:

Motoren/Speed Controller: https://www.amazon.de/1000KV-Brushless-Motors-Motor-Controller-Flugzeuge-Quadcopter/dp/B00CTDLX98

= 36€

Gyroscope: http://www.dx.com/p/gy-521-mpu6050-3-axis-acceleration-gyroscope-6dof-module-blue-154602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

= 3,32€

Akku 11,1V 2200mAh: http://www.dx.com/p/11-1v-2200mah-30c-li-polymer-battery-pack-for-450-helicopter-dji-phantom-1-450-quadcopter-366131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

= 20,05€

Propeller: http://www.hobbyking.com/hobbyking/store/__45370__Turnigy_DJI_and_Walkera_Style_Propeller_8x4_5_Black_CCW_4pcs_.html

= 3,01€

Potentiometer: https://www.conrad.de/de/leitplastik-potentiometer-mono-10-k-tt-electronics-ab-p160knp-0fc20-b-10-kr-1-st-452867.html

= 0,86€

Empfänger für Arduino + Fernsteuerung: http://www.dx.com/p/flysky-fs-t6-2-4ghz-6-ch-2-9-lcd-tx-transmitter-rx-receiver-radio-control-system-black-8-x-aa-178448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

= 60,53€

==> 63,24€ (ohne Fernsteuerung)

123,77€ (mit Fernsteuerung)

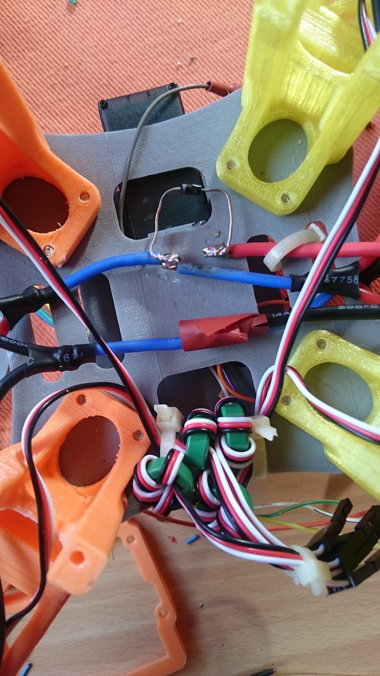
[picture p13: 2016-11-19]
images/IMG-20161025-WA0003.jpeg

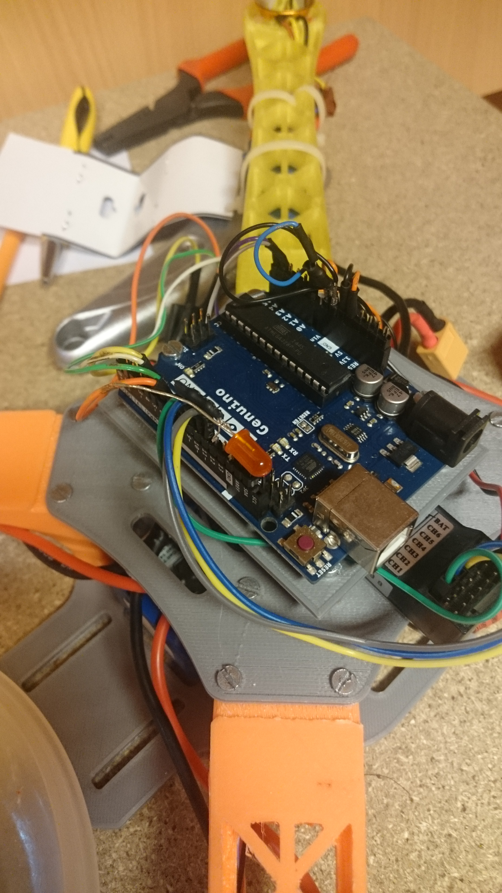
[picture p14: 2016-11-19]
images/IMG-20161030-WA0002.jpeg

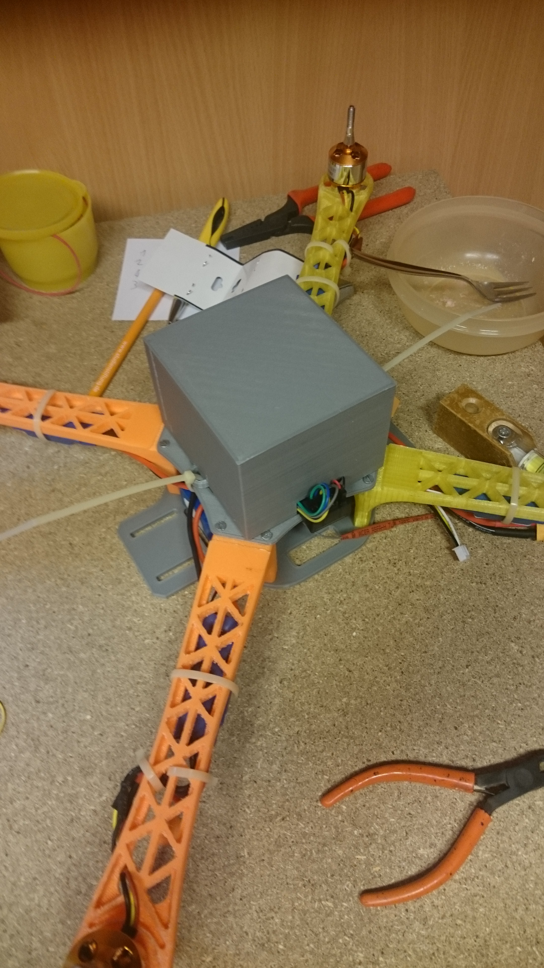
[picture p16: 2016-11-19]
images/IMG-20161030-WA0006.jpeg

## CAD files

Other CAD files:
3D Modelle/Obere Platte.skp
3D Modelle/Untere Platte.skp

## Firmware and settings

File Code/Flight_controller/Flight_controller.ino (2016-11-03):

#include <Wire.h>                          //Include the Wire.h library so we can communicate with the gyro.
#include <EEPROM.h>                        //Include the EEPROM.h library so we can store information onto the EEPROM

///////////////////////////////////////////////////////////////////////////////////////////////////////////////////////////////////////
//PID gain and limit settings
///////////////////////////////////////////////////////////////////////////////////////////////////////////////////////////////////////
float pid_p_gain_roll = 1.3;               //Gain setting for the roll P-controller
float pid_i_gain_roll = 0.04;              //Gain setting for the roll I-controller
float pid_d_gain_roll = 18.0;              //Gain setting for the roll D-controller
int pid_max_roll = 400;                    //Maximum output of the PID-controller (+/-)

float pid_p_gain_pitch = pid_p_gain_roll;  //Gain setting for the pitch P-controller.
float pid_i_gain_pitch = pid_i_gain_roll;  //Gain setting for the pitch I-controller.
float pid_d_gain_pitch = pid_d_gain_roll;  //Gain setting for the pitch D-controller.
int pid_max_pitch = pid_max_roll;          //Maximum output of the PID-controller (+/-)

float pid_p_gain_yaw = 4.0;                //Gain setting for the pitch P-controller. //4.0
float pid_i_gain_yaw = 0.02;               //Gain setting for the pitch I-controller. //0.02
float pid_d_gain_yaw = 0.0;                //Gain setting for the pitch D-controller.
int pid_max_yaw = 400;                     //Maximum output of the PID-controller (+/-)

boolean auto_level = true;                 //Auto level on (true) or off (false)

///////////////////////////////////////////////////////////////////////////////////////////////////////////////////////////////////////
//Declaring global variables
///////////////////////////////////////////////////////////////////////////////////////////////////////////////////////////////////////
byte last_channel_1, last_channel_2, last_channel_3, last_channel_4;
byte eeprom_data[36];
byte highByte, lowByte;
int receiver_input_channel_1, receiver_input_channel_2, receiver_input_channel_3, receiver_input_channel_4;
int counter_channel_1, counter_channel_2, counter_channel_3, counter_channel_4, loop_counter;
int esc_1, esc_2, esc_3, esc_4;
int throttle, battery_voltage;
int cal_int, start, gyro_address;
int receiver_input[5];
int temperature;
int acc_axis[4], gyro_axis[4];
float roll_level_adjust, pitch_level_adjust;

long acc_x, acc_y, acc_z, acc_total_vector;
unsigned long timer_channel_1, timer_channel_2, timer_channel_3, timer_channel_4, esc_timer, esc_loop_timer;
unsigned long timer_1, timer_2, timer_3, timer_4, current_time;
unsigned long loop_timer;
double gyro_pitch, gyro_roll, gyro_yaw;
double gyro_axis_cal[4];
float pid_error_temp;
float pid_i_mem_roll, pid_roll_setpoint, gyro_roll_input, pid_output_roll, pid_last_roll_d_error;
float pid_i_mem_pitch, pid_pitch_setpoint, gyro_pitch_input, pid_output_pitch, pid_last_pitch_d_error;
float pid_i_mem_yaw, pid_yaw_setpoint, gyro_yaw_input, pid_output_yaw, pid_last_yaw_d_error;
float angle_roll_acc, angle_pitch_acc, angle_pitch, angle_roll;
boolean gyro_angles_set;

///////////////////////////////////////////////////////////////////////////////////////////////////////////////////////////////////////
//Setup routine
///////////////////////////////////////////////////////////////////////////////////////////////////////////////////////////////////////
void setup(){
  //Serial.begin(57600);
  //Copy the EEPROM data for fast access data.
  for(start = 0; start <= 35; start++)eeprom_data[start] = EEPROM.read(start);
  start = 0;                                                                //Set start back to zero.
  gyro_address = eeprom_data[32];                                           //Store the gyro address in the variable.

  Wire.begin();                                                             //Start the I2C as master.

  TWBR = 12;                                                                //Set the I2C clock speed to 400kHz.

  //Arduino (Atmega) pins default to inputs, so they don't need to be explicitly declared as inputs.
  DDRD |= B11110000;                                                        //Configure digital poort 4, 5, 6 and 7 as output.
  DDRB |= B00110000;                                                        //Configure digital poort 12 and 13 as output.

  //Use the led on the Arduino for startup indication.
  digitalWrite(12,HIGH);                                                    //Turn on the warning led.

  //Check the EEPROM signature to make sure that the setup program is executed.
  while(eeprom_data[33] != 'J' || eeprom_data[34] != 'M' || eeprom_data[35] != 'B')delay(10);

  //The flight controller needs the MPU-6050 with gyro and accelerometer
  //If setup is completed without MPU-6050 stop the flight controller program  
  if(eeprom_data[31] == 2 || eeprom_data[31] == 3)delay(10);

  set_gyro_registers();                                                     //Set the specific gyro registers.

  for (cal_int = 0; cal_int < 1250 ; cal_int ++){                           //Wait 5 seconds before continuing.
    PORTD |= B11110000;                                                     //Set digital poort 4, 5, 6 and 7 high.
    delayMicroseconds(1000);                                                //Wait 1000us.
    PORTD &= B00001111;                                                     //Set digital poort 4, 5, 6 and 7 low.
    delayMicroseconds(3000);                                                //Wait 3000us.
  }

  //Let's take multiple gyro data samples so we can determine the average gyro offset (calibration).
  for (cal_int = 0; cal_int < 2000 ; cal_int ++){                           //Take 2000 readings for calibration.
    if(cal_int % 15 == 0)digitalWrite(12, !digitalRead(12));                //Change the led status to indicate calibration.
    gyro_signalen();                                                        //Read the gyro output.
    gyro_axis_cal[1] += gyro_axis[1];                                       //Ad roll value to gyro_roll_cal.
    gyro_axis_cal[2] += gyro_axis[2];                                       //Ad pitch value to gyro_pitch_cal.
    gyro_axis_cal[3] += gyro_axis[3];                                       //Ad yaw value to gyro_yaw_cal.
    //We don't want the esc's to be beeping annoyingly. So let's give them a 1000us puls while calibrating the gyro.
    PORTD |= B11110000;                                                     //Set digital poort 4, 5, 6 and 7 high.
    delayMicroseconds(1000);                                                //Wait 1000us.
    PORTD &= B00001111;                                                     //Set digital poort 4, 5, 6 and 7 low.
    delay(3);                                                               //Wait 3 milliseconds before the next loop.
  }
  //Now that we have 2000 measures, we need to devide by 2000 to get the average gyro offset.
  gyro_axis_cal[1] /= 2000;                                                 //Divide the roll total by 2000.
  gyro_axis_cal[2] /= 2000;                                                 //Divide the pitch total by 2000.
  gyro_axis_cal[3] /= 2000;                                                 //Divide the yaw total by 2000.

  PCICR |= (1 << PCIE0);                                                    //Set PCIE0 to enable PCMSK0 scan.
  PCMSK0 |= (1 << PCINT0);                                                  //Set PCINT0 (digital input 8) to trigger an interrupt on state change.
  PCMSK0 |= (1 << PCINT1);                                                  //Set PCINT1 (digital input 9)to trigger an interrupt on state change.
  PCMSK0 |= (1 << PCINT2);                                                  //Set PCINT2 (digital input 10)to trigger an interrupt on state change.
  PCMSK0 |= (1 << PCINT3);                                                  //Set PCINT3 (digital input 11)to trigger an interrupt on state change.

  //Wait until the receiver is active and the throtle is set to the lower position.
  while(receiver_input_channel_3 < 990 || receiver_input_channel_3 > 1020 || receiver_input_channel_4 < 1400){
    receiver_input_channel_3 = convert_receiver_channel(3);                 //Convert the actual receiver signals for throttle to the standard 1000 - 2000us
    receiver_input_channel_4 = convert_receiver_channel(4);                 //Convert the actual receiver signals for yaw to the standard 1000 - 2000us
    start ++;                                                               //While waiting increment start whith every loop.
    //We don't want the esc's to be beeping annoyingly. So let's give them a 1000us puls while waiting for the receiver inputs.
    PORTD |= B11110000;                                                     //Set digital poort 4, 5, 6 and 7 high.
    delayMicroseconds(1000);                                                //Wait 1000us.
    PORTD &= B00001111;                                                     //Set digital poort 4, 5, 6 and 7 low.
    delay(3);                                                               //Wait 3 milliseconds before the next loop.
    if(start == 125){                                                       //Every 125 loops (500ms).
      digitalWrite(12, !digitalRead(12));                                   //Change the led status.
      start = 0;                                                            //Start again at 0.
    }
  }
  start = 0;                                                                //Set start back to 0.

  //Load the battery voltage to the battery_voltage variable.
  //65 is the voltage compensation for the diode.
  //12.6V equals ~5V @ Analog 0.
  //12.6V equals 1023 analogRead(0).
  //1260 / 1023 = 1.2317.
  //The variable battery_voltage holds 1050 if the battery voltage is 10.5V.
  battery_voltage = (analogRead(0) + 65) * 1.2317;

  loop_timer = micros();                                                    //Set the timer for the next loop.

  //When everything is done, turn off the led.
  digitalWrite(12,LOW);                                                     //Turn off the warning led.
}
///////////////////////////////////////////////////////////////////////////////////////////////////////////////////////////////////////
//Main program loop
///////////////////////////////////////////////////////////////////////////////////////////////////////////////////////////////////////
void loop(){

  //65.5 = 1 deg/sec (check the datasheet of the MPU-6050 for more information).
  gyro_roll_input = (gyro_roll_input * 0.7) + ((gyro_roll / 65.5) * 0.3);   //Gyro pid input is deg/sec.
  gyro_pitch_input = (gyro_pitch_input * 0.7) + ((gyro_pitch / 65.5) * 0.3);//Gyro pid input is deg/sec.
  gyro_yaw_input = (gyro_yaw_input * 0.7) + ((gyro_yaw / 65.5) * 0.3);      //Gyro pid input is deg/sec.

  //Gyro angle calculations
  //0.0000611 = 1 / (250Hz / 65.5)
  angle_pitch += gyro_pitch * 0.0000611;                                    //Calculate the traveled pitch angle and add this to the angle_pitch variable.
  angle_roll += gyro_roll * 0.0000611;                                      //Calculate the traveled roll angle and add this to the angle_roll variable.

  //0.000001066 = 0.0000611 * (3.142(PI) / 180degr) The Arduino sin function is in radians
  angle_pitch -= angle_roll * sin(gyro_yaw * 0.000001066);                  //If the IMU has yawed transfer the roll angle to the pitch angel.
  angle_roll += angle_pitch * sin(gyro_yaw * 0.000001066);                  //If the IMU has yawed transfer the pitch angle to the roll angel.

  //Accelerometer angle calculations
  acc_total_vector = sqrt((acc_x*acc_x)+(acc_y*acc_y)+(acc_z*acc_z));       //Calculate the total accelerometer vector.
  
  if(abs(acc_y) < acc_total_vector){                                        //Prevent the asin function to produce a NaN
    angle_pitch_acc = asin((float)acc_y/acc_total_vector)* 57.296;          //Calculate the pitch angle.
  }
  if(abs(acc_x) < acc_total_vector){                                        //Prevent the asin function to produce a NaN
    angle_roll_acc = asin((float)acc_x/acc_total_vector)* -57.296;          //Calculate the roll angle.
  }
  
  //Place the MPU-6050 spirit level and note the values in the following two lines for calibration.
  angle_pitch_acc -= 0.0;                                                   //Accelerometer calibration value for pitch.
  angle_roll_acc -= 0.0;                                                    //Accelerometer calibration value for roll.
  
  angle_pitch = angle_pitch * 0.9996 + angle_pitch_acc * 0.0004;            //Correct the drift of the gyro pitch angle with the accelerometer pitch angle.
  angle_roll = angle_roll * 0.9996 + angle_roll_acc * 0.0004;               //Correct the drift of the gyro roll angle with the accelerometer roll angle.

  pitch_level_adjust = angle_pitch * 15;                                    //Calculate the pitch angle correction
  roll_level_adjust = angle_roll * 15;                                      //Calculate the roll angle correction

  if(!auto_level){                                                          //If the quadcopter is not in auto-level mode
    pitch_level_adjust = 0;                                                 //Set the pitch angle correction to zero.
    roll_level_adjust = 0;                                                  //Set the roll angle correcion to zero.
  }


  //For starting the motors: throttle low and yaw left (step 1).
  if(receiver_input_channel_3 < 1050 && receiver_input_channel_4 < 1050)start = 1;
  //When yaw stick is back in the center position start the motors (step 2).
  if(start == 1 && receiver_input_channel_3 < 1050 && receiver_input_channel_4 > 1450){
    start = 2;

    angle_pitch = angle_pitch_acc;                                          //Set the gyro pitch angle equal to the accelerometer pitch angle when the quadcopter is started.
    angle_roll = angle_roll_acc;                                            //Set the gyro roll angle equal to the accelerometer roll angle when the quadcopter is started.
    gyro_angles_set = true;                                                 //Set the IMU started flag.

    //Reset the PID controllers for a bumpless start.
    pid_i_mem_roll = 0;
    pid_last_roll_d_error = 0;
    pid_i_mem_pitch = 0;
    pid_last_pitch_d_error = 0;
    pid_i_mem_yaw = 0;
    pid_last_yaw_d_error = 0;
  }
  //Stopping the motors: throttle low and yaw right.
  if(start == 2 && receiver_input_channel_3 < 1050 && receiver_input_channel_4 > 1950)start = 0;

  //The PID set point in degrees per second is determined by the roll receiver input.
  //In the case of deviding by 3 the max roll rate is aprox 164 degrees per second ( (500-8)/3 = 164d/s ).
  pid_roll_setpoint = 0;
  //We need a little dead band of 16us for better results.
  if(receiver_input_channel_1 > 1508)pid_roll_setpoint = receiver_input_channel_1 - 1508;
  else if(receiver_input_channel_1 < 1492)pid_roll_setpoint = receiver_input_channel_1 - 1492;

  pid_roll_setpoint -= roll_level_adjust;                                   //Subtract the angle correction from the standardized receiver roll input value.
  pid_roll_setpoint /= 3.0;                                                 //Divide the setpoint for the PID roll controller by 3 to get angles in degrees.


  //The PID set point in degrees per second is determined by the pitch receiver input.
  //In the case of deviding by 3 the max pitch rate is aprox 164 degrees per second ( (500-8)/3 = 164d/s ).
  pid_pitch_setpoint = 0;
  //We need a little dead band of 16us for better results.
  if(receiver_input_channel_2 > 1508)pid_pitch_setpoint = receiver_input_channel_2 - 1508;
  else if(receiver_input_channel_2 < 1492)pid_pitch_setpoint = receiver_input_channel_2 - 1492;

  pid_pitch_setpoint -= pitch_level_adjust;                                  //Subtract the angle correction from the standardized receiver pitch input value.
  pid_pitch_setpoint /= 3.0;                                                 //Divide the setpoint for the PID pitch controller by 3 to get angles in degrees.

  //The PID set point in degrees per second is determined by the yaw receiver input.
  //In the case of deviding by 3 the max yaw rate is aprox 164 degrees per second ( (500-8)/3 = 164d/s ).
  pid_yaw_setpoint = 0;
  //We need a little dead band of 16us for better results.
  if(receiver_input_channel_3 > 1050){ //Do not yaw when turning off the motors.
    if(receiver_input_channel_4 > 1508)pid_yaw_setpoint = (receiver_input_channel_4 - 1508)/3.0;
    else if(receiver_input_channel_4 < 1492)pid_yaw_setpoint = (receiver_input_channel_4 - 1492)/3.0;
  }
  
  calculate_pid();                                                            //PID inputs are known. So we can calculate the pid output.

  //The battery voltage is needed for compensation.
  //A complementary filter is used to reduce noise.
  //0.09853 = 0.08 * 1.2317.
  battery_voltage = battery_voltage * 0.92 + (analogRead(0) + 65) * 0.09853;

  //Turn on the led if battery voltage is to low.
  if(battery_voltage < 1000 && battery_voltage > 600)digitalWrite(12, HIGH);


  throttle = receiver_input_channel_3;                                      //We need the throttle signal as a base signal.

  if (start == 2){                                                          //The motors are started.
    if (throttle > 1800) throttle = 1800;                                   //We need some room to keep full control at full throttle.
    esc_1 = throttle - pid_output_pitch + pid_output_roll - pid_output_yaw; //Calculate the pulse for esc 1 (front-right - CCW)
    esc_2 = throttle + pid_output_pitch + pid_output_roll + pid_output_yaw; //Calculate the pulse for esc 2 (rear-right - CW)
    esc_3 = throttle + pid_output_pitch - pid_output_roll - pid_output_yaw; //Calculate the pulse for esc 3 (rear-left - CCW)
    esc_4 = throttle - pid_output_pitch - pid_output_roll + pid_output_yaw; //Calculate the pulse for esc 4 (front-left - CW)

    if (battery_voltage < 1240 && battery_voltage > 800){                   //Is the battery connected?
      esc_1 += esc_1 * ((1240 - battery_voltage)/(float)3500);              //Compensate the esc-1 pulse for voltage drop.
      esc_2 += esc_2 * ((1240 - battery_voltage)/(float)3500);              //Compensate the esc-2 pulse for voltage drop.
      esc_3 += esc_3 * ((1240 - battery_voltage)/(float)3500);              //Compensate the esc-3 pulse for voltage drop.
      esc_4 += esc_4 * ((1240 - battery_voltage)/(float)3500);              //Compensate the esc-4 pulse for voltage drop.
    } 

    if (esc_1 < 1200) esc_1 = 1200;                                         //Keep the motors running.
    if (esc_2 < 1200) esc_2 = 1200;                                         //Keep the motors running.
    if (esc_3 < 1200) esc_3 = 1200;                                         //Keep the motors running.
    if (esc_4 < 1200) esc_4 = 1200;                                         //Keep the motors running.

    if(esc_1 > 2000)esc_1 = 2000;                                           //Limit the esc-1 pulse to 2000us.
    if(esc_2 > 2000)esc_2 = 2000;                                           //Limit the esc-2 pulse to 2000us.
    if(esc_3 > 2000)esc_3 = 2000;                                           //Limit the esc-3 pulse to 2000us.
    if(esc_4 > 2000)esc_4 = 2000;                                           //Limit the esc-4 pulse to 2000us.  
  }

  else{
    esc_1 = 1000;                                                           //If start is not 2 keep a 1000us pulse for ess-1.
    esc_2 = 1000;                                                           //If start is not 2 keep a 1000us pulse for ess-2.
    esc_3 = 1000;                                                           //If start is not 2 keep a 1000us pulse for ess-3.
    esc_4 = 1000;                                                           //If start is not 2 keep a 1000us pulse for ess-4.
  }

    
  if(micros() - loop_timer > 4050)digitalWrite(12, HIGH);                   //Turn on the LED if the loop time exceeds 4050us.
  
  //All the information for controlling the motor's is available.
  //The refresh rate is 250Hz. That means the esc's need there pulse every 4ms.
  while(micros() - loop_timer < 4000);                                      //We wait until 4000us are passed.
  loop_timer = micros();                                                    //Set the timer for the next loop.

  PORTD |= B11110000;                                                       //Set digital outputs 4,5,6 and 7 high.
  timer_channel_1 = esc_1 + loop_timer;                                     //Calculate the time of the faling edge of the esc-1 pulse.
  timer_channel_2 = esc_2 + loop_timer;                                     //Calculate the time of the faling edge of the esc-2 pulse.
  timer_channel_3 = esc_3 + loop_timer;                                     //Calculate the time of the faling edge of the esc-3 pulse.
  timer_channel_4 = esc_4 + loop_timer;                                     //Calculate the time of the faling edge of the esc-4 pulse.
  
  //There is always 1000us of spare time. So let's do something usefull that is very time consuming.
  //Get the current gyro and receiver data and scale it to degrees per second for the pid calculations.
  gyro_signalen();
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

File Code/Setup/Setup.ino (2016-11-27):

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
#include <Wire.h>               //Include the Wire.h library so we can communicate with the gyro
#include <EEPROM.h>             //Include the EEPROM.h library so we can store information onto the EEPROM

//Declaring Global Variables
byte last_channel_1, last_channel_2, last_channel_3, last_channel_4;
byte lowByte, highByte, type, gyro_address, error, clockspeed_ok;
byte channel_1_assign, channel_2_assign, channel_3_assign, channel_4_assign;
byte roll_axis, pitch_axis, yaw_axis;
byte receiver_check_byte, gyro_check_byte;
volatile int receiver_input_channel_1, receiver_input_channel_2, receiver_input_channel_3, receiver_input_channel_4;
int center_channel_1, center_channel_2, center_channel_3, center_channel_4;
int high_channel_1, high_channel_2, high_channel_3, high_channel_4;
int low_channel_1, low_channel_2, low_channel_3, low_channel_4;
int address, cal_int;
unsigned long timer, timer_1, timer_2, timer_3, timer_4, current_time;
float gyro_pitch, gyro_roll, gyro_yaw;
float gyro_roll_cal, gyro_pitch_cal, gyro_yaw_cal;


//Setup routine
void setup(){
  pinMode(12, OUTPUT);
  //Arduino (Atmega) pins default to inputs, so they don't need to be explicitly declared as inputs
  PCICR |= (1 << PCIE0);    // set PCIE0 to enable PCMSK0 scan
  PCMSK0 |= (1 << PCINT0);  // set PCINT0 (digital input 8) to trigger an interrupt on state change
  PCMSK0 |= (1 << PCINT1);  // set PCINT1 (digital input 9)to trigger an interrupt on state change
  PCMSK0 |= (1 << PCINT2);  // set PCINT2 (digital input 10)to trigger an interrupt on state change
  PCMSK0 |= (1 << PCINT3);  // set PCINT3 (digital input 11)to trigger an interrupt on state change
  Wire.begin();             //Start the I2C as master
  Serial.begin(57600);      //Start the serial connetion @ 57600bps
  delay(250);               //Give the gyro time to start 
}
//Main program
void loop(){
  
  Serial.println(F(""));
  Serial.println(F("==================================================="));
  Serial.println(F("System check"));
  Serial.println(F("==================================================="));
  delay(1000);
  Serial.println(F("Checking I2C clock speed."));
  delay(1000);
  
  TWBR = 12;                      //Set the I2C clock speed to 400kHz.
  
  #if F_CPU == 16000000L          //If the clock speed is 16MHz include the next code line when compiling
    clockspeed_ok = 1;            //Set clockspeed_ok to 1
  #endif                          //End of if statement

  if(TWBR == 12 && clockspeed_ok){
    Serial.println(F("I2C clock speed is correctly set to 400kHz."));
  }
  else{
    Serial.println(F("I2C clock speed is not set to 400kHz. (ERROR 8)"));
    error = 1;
  }
  
  if(error == 0){
    Serial.println(F(""));
    Serial.println(F("==================================================="));
    Serial.println(F("Transmitter setup"));
    Serial.println(F("==================================================="));
    delay(1000);
    Serial.print(F("Checking for valid receiver signals."));
    //Wait 10 seconds until all receiver inputs are valid
    wait_for_receiver();
    Serial.println(F(""));
  }
  //Quit the program in case of an error
  if(error == 0){
    delay(2000);
    Serial.println(F("Place all sticks and subtrims in the center position within 10 seconds."));
    for(int i = 9;i > 0;i--){
      delay(1000);
      Serial.print(i);
      Serial.print(" ");
    }
    Serial.println(" ");
    //Store the central stick positions
    center_channel_1 = receiver_input_channel_1;
    center_channel_2 = receiver_input_channel_2;
    center_channel_3 = receiver_input_channel_3;
    center_channel_4 = receiver_input_channel_4;
    Serial.println(F(""));
    Serial.println(F("Center positions stored."));
    Serial.print(F("Digital input 08 = "));
    Serial.println(receiver_input_channel_1);
    Serial.print(F("Digital input 09 = "));
    Serial.println(receiver_input_channel_2);
    Serial.print(F("Digital input 10 = "));
    Serial.println(receiver_input_channel_3);
    Serial.print(F("Digital input 11 = "));
    Serial.println(receiver_input_channel_4);
    Serial.println(F(""));
    Serial.println(F(""));
  }
  if(error == 0){  
    Serial.println(F("Move the throttle stick to full throttle and back to center"));
    //Check for throttle movement
    check_receiver_inputs(1);
    Serial.print(F("Throttle is connected to digital input "));
    Serial.println((channel_3_assign & 0b00000111) + 7);
    if(channel_3_assign & 0b10000000)Serial.println(F("Channel inverted = yes"));
    else Serial.println(F("Channel inverted = no"));
    wait_sticks_zero();
    
    Serial.println(F(""));
    Serial.println(F(""));
    Serial.println(F("Move the roll stick to simulate left wing up and back to center"));
    //Check for throttle movement
    check_receiver_inputs(2);
    Serial.print(F("Roll is connected to digital input "));
    Serial.println((channel_1_assign & 0b00000111) + 7);
    if(channel_1_assign & 0b10000000)Serial.println(F("Channel inverted = yes"));
    else Serial.println(F("Channel inverted = no"));
    wait_sticks_zero();
  }
  if(error == 0){
    Serial.println(F(""));
    Serial.println(F(""));
    Serial.println(F("Move the pitch stick to simulate nose up and back to center"));
    //Check for throttle movement
    check_receiver_inputs(3);
    Serial.print(F("Pitch is connected to digital input "));
    Serial.println((channel_2_assign & 0b00000111) + 7);
    if(channel_2_assign & 0b10000000)Serial.println(F("Channel inverted = yes"));
    else Serial.println(F("Channel inverted = no"));
    wait_sticks_zero();
  }
  if(error == 0){
    Serial.println(F(""));
    Serial.println(F(""));
    Serial.println(F("Move the yaw stick to simulate nose right and back to center"));
    //Check for throttle movement
    check_receiver_inputs(4);
    Serial.print(F("Yaw is connected to digital input "));
    Serial.println((channel_4_assign & 0b00000111) + 7);
    if(channel_4_assign & 0b10000000)Serial.println(F("Channel inverted = yes"));
    else Serial.println(F("Channel inverted = no"));
    wait_sticks_zero();
  }
  if(error == 0){
    Serial.println(F(""));
    Serial.println(F(""));
    Serial.println(F("Gently move all the sticks simultaneously to their extends"));
    Serial.println(F("When ready put the sticks back in their center positions"));
    //Register the min and max values of the receiver channels
    register_min_max();
    Serial.println(F(""));
    Serial.println(F(""));
    Serial.println(F("High, low and center values found during setup"));
    Serial.print(F("Digital input 08 values:"));
    Serial.print(low_channel_1);
    Serial.print(F(" - "));
    Serial.print(center_channel_1);
    Serial.print(F(" - "));
    Serial.println(high_channel_1);
    Serial.print(F("Digital input 09 values:"));
    Serial.print(low_channel_2);
    Serial.print(F(" - "));
    Serial.print(center_channel_2);
    Serial.print(F(" - "));
    Serial.println(high_channel_2);
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

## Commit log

2016-09-29 Motor und Empfänger Test Sketch
2016-11-27 Umstrukturierung des repositories
2016-12-05 Schematics für html
